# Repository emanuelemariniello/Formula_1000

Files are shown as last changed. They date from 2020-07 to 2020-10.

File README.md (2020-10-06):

# Formula_1000
The aim of this project is to design from scratch a Formula 1000 racing car using mainly standard components easily founded in the market. The design is guided following the F1000 regulations of 2013 and the UNI and ISO design standards. There are different software used during the project, such as Creo, Solidworks, Catia V5 and Siemens NX as CAD software, Matlab and PyCharm as mathematical solver and Ansys Workbench and Altair HyperWorks as FEA software.

# How to use

A full detailed report on the project is in the following link: (https://github.com/emanuelemariniello/Formula_1000/blob/master/Report/Report.pdf).

Python is needed to be installed in your machine.

Download the project and run the file Index.bat and follow the instructions on the terminal to visualize the main design variables related to the different components.

# Overview

### Gearbox Overview
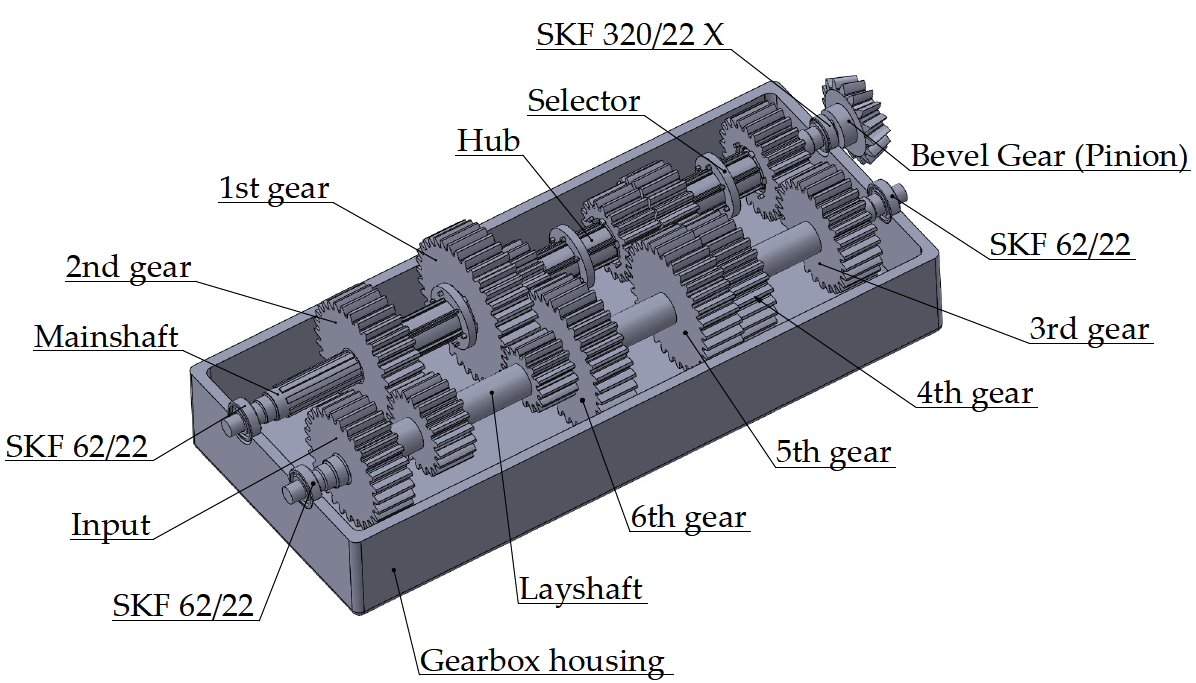
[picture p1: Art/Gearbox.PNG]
Gearbox Overview

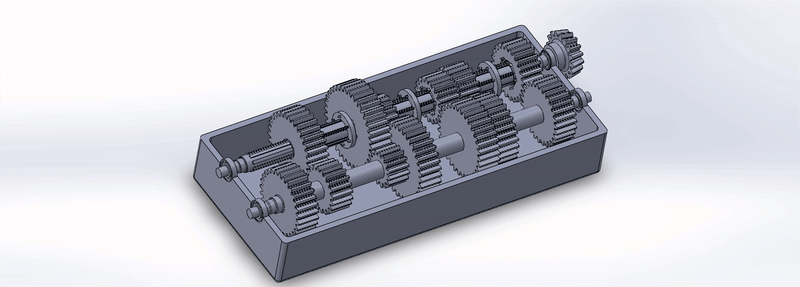
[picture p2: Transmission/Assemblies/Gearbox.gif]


### Open Differential Overview
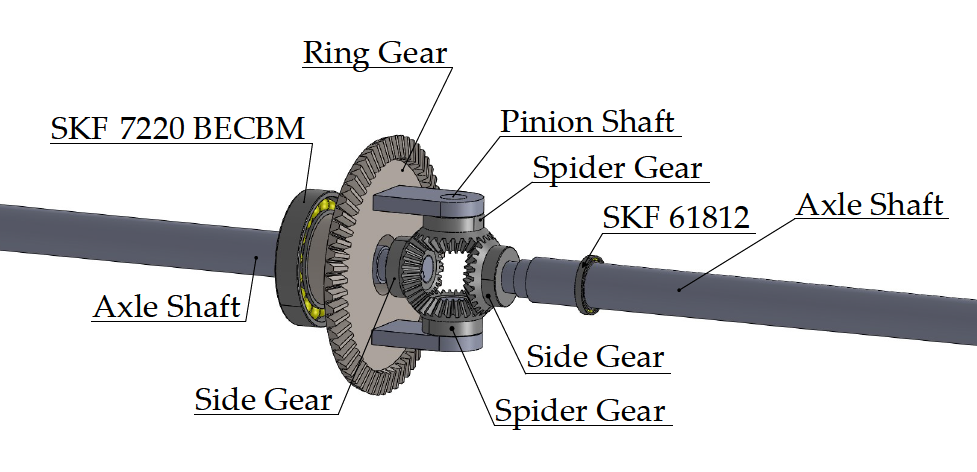
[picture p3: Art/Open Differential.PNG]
Open Differential Overview


### Transmission Overview
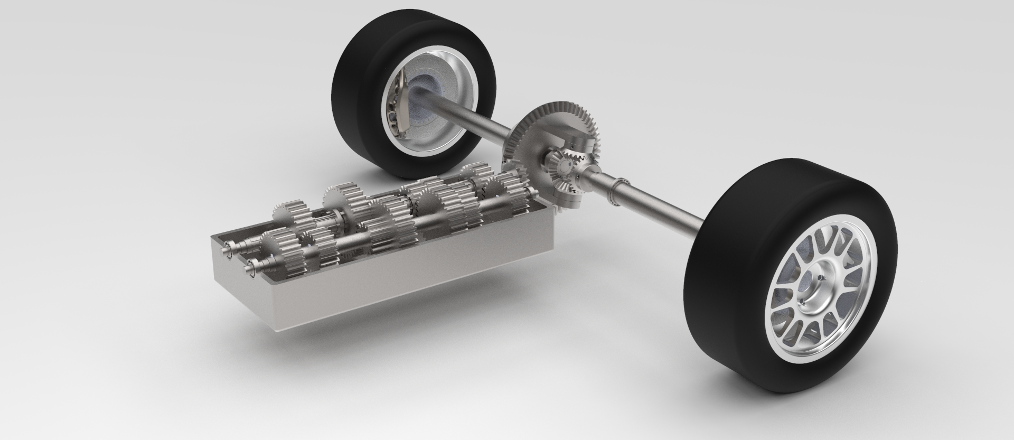
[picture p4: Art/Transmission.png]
Transmission Overview


### Suspensions Overview
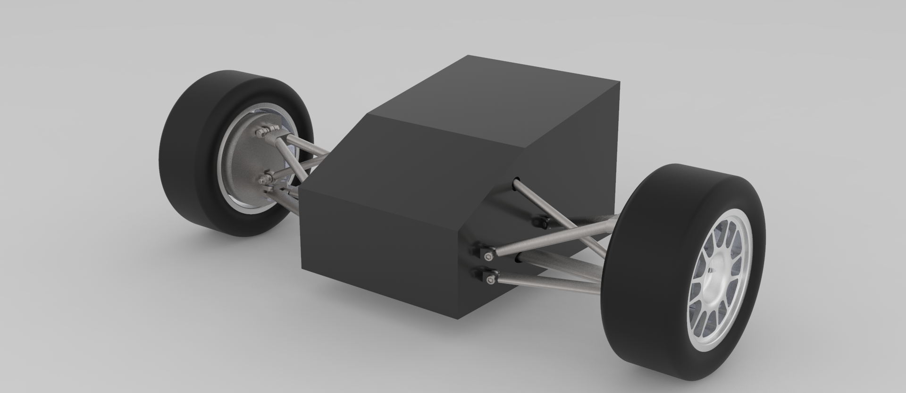
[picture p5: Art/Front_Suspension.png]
Front Suspension Overview

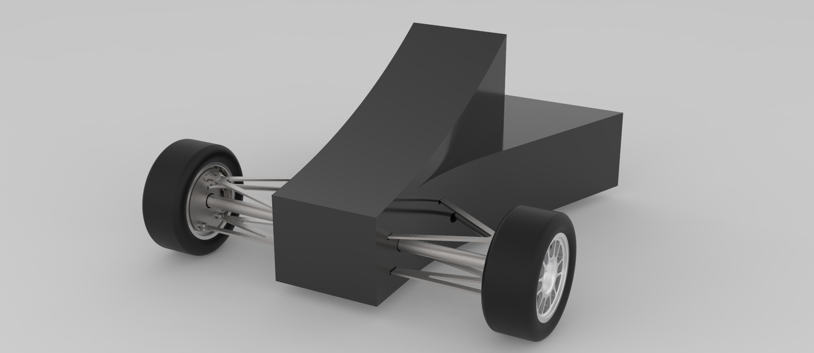
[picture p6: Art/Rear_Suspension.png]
Rear Suspension Overview


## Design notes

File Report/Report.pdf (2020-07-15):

# Design from scratch of a Formula 1000 racing car

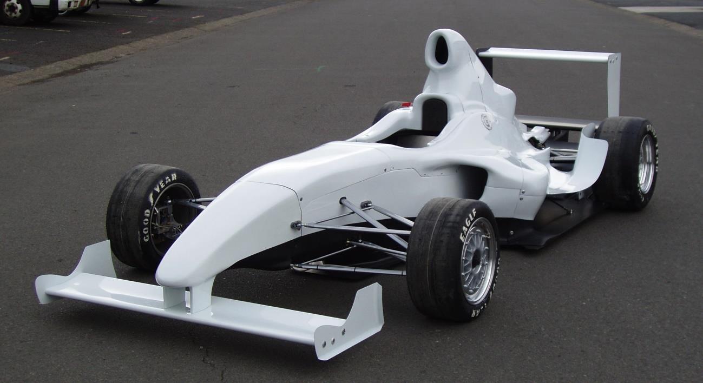
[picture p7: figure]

## Author:

## Emanuele Mariniello

I

## Abstract

The aim of this project is to design from scratch a Formula 1000 racing car using mainly standard components easily founded in the market.
The design is guided following the F1000 regulations of 2013 and the UNI and ISO design standards.
There are different software used during the project, such as Creo, Solidworks, Catia V5 and Siemens NX as CAD software, Matlab and PyCharm as mathematical solver and Ansys Workbench and Altair HyperWorks as FEA software.

II

## Contents

III

## List of Acronyms

- F1000 = Formula 1000
- Kph = Kilometres per hour
- g.r. = Gear ratio
- rpm = Rotation per minut
- TBD = To be defined

Design from scratch of a Formula 1000 racing car

Introduction | 1

## 1. Introduction

Formula 1000 is an open wheel class of Formula car racing, with professional and amateur series worldwide. Formula 1000 gets its name from the 1000 cc superbike engine used to power a single seat, open wheel race car with fully adjustable wings and suspension. The F1000 class, known in SCCA as FB, is similar to racing classes FA (Formula Atlantic) and FC (Formula Continental). In the United States, Formula 1000 races in the North American Formula 1000 Championship presented by American Racer Tire as well as SCCA amateur competition.

Formula 1000 RaceCars can reach speeds in excess of 270 kph; brake and corner beyond 3 g's; and provide a challenge to any driver, engineer, or team.

Figure 1-1 Formula 1000 car [2].

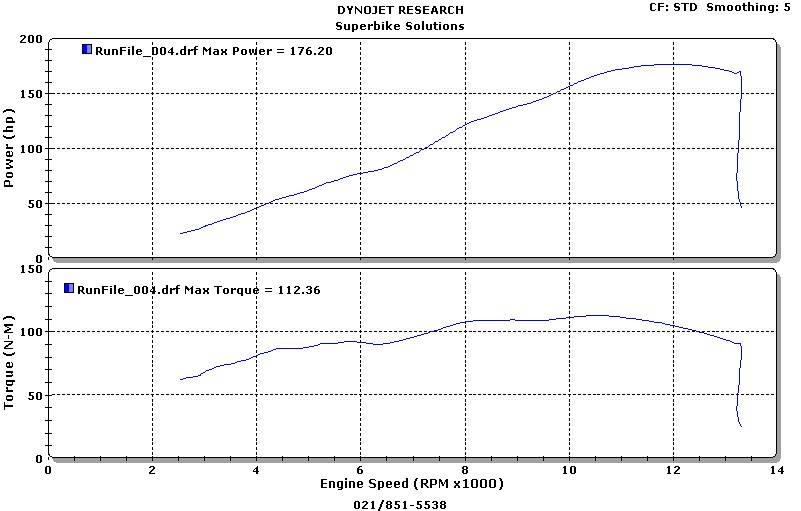
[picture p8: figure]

Engine | 2

## 2. Engine

Following the F1000 regulation of 2013 [1] there are 4 engines that it is possible to select for the racing car, they are:

- Kawasaki ZX10R 1000
- Suzuki GSXR 1000
- Yamaha YZF R1
- Honda CBR 1000 RR

Honda CBR 1000 RR is the engine selected for this project, following there are all the specifications:

Table 1 - CBR 1000 RR Engine specs [4].

Figure 2-1 Dyno chart 2014 CBR1000RR [3].

Capacity | 999.8 cc / 61 cu-cu-in
Bore x Stroke | 76 x 55.1 mm
Cooling System | Liquid cooled
Compression Ratio | 12.3:1
Oil Capacity | 3.7 Litres
Max Power | 133 kW / 178 hp @ 12250rpm
Max Torque | 114 Nm / 84.07 ft.lb @ 10500rpm

Trasmission | 3

## 3. Trasmission

## Sequential Gearbox

Typically a sequential gearbox is installed in racing cars, in this project a sequential gearbox with 6th gears (no reverse gear) is going to be designed using commercial components.

## Design

## 3.1.1.1 Gears

Once decided the engine, it is possible to start to design the sequential gearbox.

Figure 3-1 Overview of the sequential gearbox system [6].
The design of it starts calculating the peak torque at the rear wheels, a python code was created to perform this operation by following the procedure described below, to open it just run the file Index.bat in the main folder and select the following path in the script: Trasmission → Gearbox → Gear ratio.
Defining W as the weight of the racing car, L is the wheelbase and Lr as the distance of the center of mass from the rear wheel (this value in this case is an assumption using as reference a real F1 car) [5], them numerically are equivalent to:

W = 490 ∗ 9.81 = 4806,9 [N]; L = 3500 [mm] Lr = 1787,5 [mm]

From these data, the Static rear axle load WR and the Static front axle load WF are determined:

WR = W ∗

Lr
L

= 4806,9 ∗

1787,5
3250 ≅ 2643,80 [N] | (1)

WF = W ∗

LL
L

= 4806,9 ∗

1462,5
3250 ≅ 2163,10 [N] | (2)

Consequential the Traction force is equal to:

F =

WR ∗ μ

1 −

ℎm ∗ μ
L

=

2643,80 ∗ 1,2

1 −

325 ∗ 1,2
3250
≅ 3605,175 [N] | (3)

Where, μ is the average coefficient of friction between wheels and the road while ℎm is the height of the centre of mass.
Next step is to evaluate the longitudinal load transfer ΔWx:

ΔWx = +̅

F ∗ ℎm
L

= +̅

3605,175 ∗ 325
3250 | ≅ ±360,52 [N] | (4)

So, the Rear wheel loads WRR and WRL are equal to:

WRR, WRL =

WR + ΔWx
2

=

2643,80 + 360,52
2

≅ 1502,16 [N] (5)

While the Front wheel loads WFR and WFL are equal to:

WFR, WFL =

WF − ΔWx
2

=

2163,10 − 466,55
2

≅ 901,3 [N]

(6)

Now it is possible to evaluate the Peak torque rear wheels Twℎeels:

T_wℎeels = (W_RR + W_RL ) ∗ r_w ∗ μ = (1502,15 + 1502,15) ∗ 0,33 ∗ 1,2 ≅ 1190,43 [Nm]

(7)

Twℎeels, is very important because from it starts the defining of the gear ratios of the gear system beginning from the 1st gear ratio.

First thing is to define the minimum total 1st gear ratio, between the engine crankshaft and the wheel driveshafts, able to provide enough torque to the wheels in order to start the movement of the racing car; to do so, the following equation is used:

min total 1

stgear ratio =

Twℎeels

TEngine

(8)

Twℎeels is already defined, TEngine is defined analyzing the engine Dyno chart (Figure 2-1). This value is selected thinking at the torque provided by the engine and at which range of rpm it is available.
This range needs to be big enough to help the driver, at the starting race, to do not have that the car shuts down, but at the same time, this ratio does not need to be too small otherwise the top speed of the 1st gear is low.

Figure 3-2 Tengine Selection.
Selecting TEngine equal to 100 Nm, as it is possible to observe in the Figure 3-2, the rpm range is quite big (from around 7500 rpm to around 12500 rpm) so the engine within this range will provide enough torque and the driver, at the starting of the race, with a proper gear ratio, it will be able to start the race without any problem.
So the minimum total 1st gear ratio is equivalent to:

min total 1

stgear ratio =

Twℎeels

TEngine

=

1190
100 = 11,9 | (9)

The total gear ratio, in the gearbox, is evaluated multiplying every gear ratio per each coupling of gear wheels active; each engaged gear has inside this multiplication the primary gear reduction, between input shaft from the engine and the layshaft (connection visible in the Figure 3-3), the gear ratio of the differential and the relative coupling of gear wheels associated to the gear engaged.

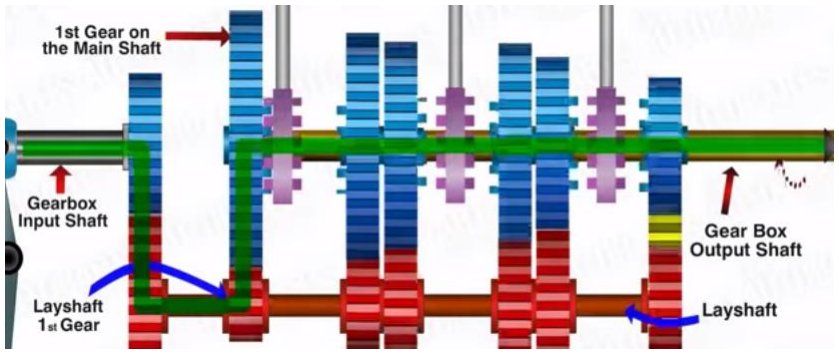
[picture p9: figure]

Figure 3-3 Example of 1

st gear inserted [6].

Using as a reference the same kinds of gearboxes, both the gear ratio of the primary reduction (ipr) and the differential (idifferential) are fixed respectively to 1,8125 and 3,5625, so from these ratios it is possible to find the minimum gear ratio required engaging the 1st gear.

min 1

stgear ratio =

min total 1

stg. r.

(ipr) ∗ (idifferential)

=

11,9
1,8125 ∗ 3,5625
≅ 1,84

(10)

The racing cars use spur gears, also if they tend to vibrate and become noisy at higher speeds, not so important compared to the fact that they have a better way to transmit torque compared to helical gears.
So fixing helix angle β=0° and the pressure angle α=20°
, with the Table 2 is it
possible knowing the gear ratio (u in this table) the minimum number of teeth required for the gears with external teeth (in Italian “Dentatura esterna”), in this case the number is equal to 15, so z1, which represents the number of teeth of the driving gear, is set as 15.

Table 2 - Minimum number of teeth spur gear [7].

The gear ratio (defined as i) selected is 2,4:

z2 = i ∗ z1 = 2,4 ∗ 15 = 36 | (11)

Check that the total 1st gear ratio is greater than the minimum value:

Total 1

stgear ratio = (ipr) ∗ (idifferential) ∗ (i1
st)
= 1,8125 ∗ 3,5625 ∗ 2,4 ≅ 15,4969 > 15,41 | (12)

From this point, it is possible to define the other ratios thinking mainly, but not only, about at which speed the driven reaches before changing gear. The maximum speed, so also the point when it is better to change gear, is reached when the engine is able to provide the maximum torque, in the Honda CBR 1000 RR this happens when it reaches around 13000 rpm (Figure 2-1).
An estimation of the speed that the vehicle can reach at that moment for each gear engaged, can be done using this formula, in this cased used for the 1st gear:

Max speed 1

stgear =

Max power rpm ∗ π ∗ Φwℎeel ∗ 60 1000 ∗ Total 1

stgear ratio = 13000 ∗ π ∗ 0,3302 ∗ 60 1000 ∗ 15,4969 ≅ 52,21 [km⁄ℎ] | (13)

Where Φwℎeel is the diameter of the wheels in meters.
As will be later explained in paragraphs 3.1.1.1.1 and 3.1.1.1.2, by calculating the minimum modulus for each gear coupling, it is established that the modulus of the all the spur gears inside the gear box is fixed at 5. An important constraint in the gearbox system is that the wheelbase between each gear coupling needs to be the same, it can be satisfied by the following calculation:

wℎeelbase 1

stgear =

module ∗ (z1 + z2)
2

=

5 ∗ (15 + 36)
2
= 127,5 [mm]

(14)

Observing the equation (14) to have the same wheelbase, having the same module, the sum of the teeth of the gears coupled must be the same everywhere in the gearbox (except for the primary reduction and the differential), in this case, the sum is equal to 15 + 36 = 51, and the gear ratio is related to the teeth with this expression:

gear ratio =

z2
z1

(15)

So playing with the constraint of the total number of teeth and the maximum speed achieved at the end of the gear before the shift, it is possible to establish every gear ratio. In the project folder called Trasmission there is an excel file called Design.xlsx where it possible to find all the operations explained before, but in the next table is represented directly the final gear ratio output established from it.

| Gear ratio | z1 | z2 | z1+z2 | wheelbase [mm]
Primary reduction | 1,8125 | 16 | 29 | 45 | 112,50
1st | 2,4000 | 15 | 36 | 51 | 127,50
2nd | 1,5500 | 20 | 31 | 51 | 127,50
3rd | 0,8889 | 27 | 24 | 51 | 127,50
4th | 0,7000 | 30 | 21 | 51 | 127,50
5th | 0,5938 | 32 | 19 | 51 | 127,50
6th | 0,5000 | 34 | 17 | 51 | 127,50
Differential | 3,5625 | TBD | TBD | TBD | -

Table 3 - Gear ratios.
At this point is possible design every gear wheel in the gearbox.

## 3.1.1.1.1 Spur Gears

In the project folder Trasmission\Gearbox\Gears\Matlab are present Matlab scripts called Design_xxx_gear.m where all the operations explained in the following paragraph are executed, the procedure design it extracted mainly from the manual “Manuale di Meccanica” [7].
The 1st gear is going to be used as an example case, also because it is the first gear connection where all the necessary data are defined.
Remembering that spur gears are used in a racing gearbox, it is possible to define the helix angle β=0° and the pressure angle α=20° and as defined before the gear ratio i = 2,4. The material selected is the steel C60 (EN 10277-5) with has the ultimate tensile strength σR = 900 [N⁄mm²], the Young modulus E = 217 [GPa]

and the Brinell hardness HB = 215 [HB].
Designing the spur gear wheels to wear-resistant, another evaluation is: how many hours the designed gearbox needs to work before it can have failures? The gearbox needs to survive at least for 6 full grand prix that is around 50 hours in total.
Everything now is specified, so the first step is to calculate the coefficient K1:

K1 ≅ 1,18 ∗ √
E1 ∗ E2
E1 + E2

= 1,18 ∗ √
217 ∗ 217
217 + 217

≅ 388,68 [

√N⁄mm] (16)

both the gear wheels are made with the same material so E1 and E2 are the same. The k constant now is calculated:

k = √
2 ∗ K1

2
z1

2
∗ sin(2 ∗ α)

∗ (1 +

z1
z2

)

3

= √
2 ∗ (388,68)

2
(15)

2 ∗ sin(2 ∗ 20)

∗ (1 +

15
36)

3

≅ 14,36 [√N⁄mm²
3
]

(17)

Now the admissible pressure on the tooth padm can be evaluated:

padm = 24,5 ∗

HB
√n1 ∗ ℎ
6 | = 24,5 ∗

215
√7172,4 ∗ 50 ⁶ | ≅ 625 [N⁄mm²] | (18)

Where ℎ is the minimum working hours of the gearbox, defined before, and n1 is the rotational speed in rpm that is calculated from the gearbox input shaft:

n1 =

ni

ipr

=

13000
1,8125 ≅ 7172,4 [rpm] | (19)

So now it is possible to calculate the minimum module that the gear wheels need to have:

mmin = k ∗ √
T ∗ cos²(β)

λ ∗ padm

2

3

= 14,36 ∗ √
114000 ∗ cos²(0)
10 ∗ (625)

2

3
≅ 4,42 (20)

Where T in the torque provided by the engine in [N ∗ mm] and λ =

b
m

= 10,
where m is module and b is the width of the gear wheels (Figure 3-4). Selecting the module equal to 5, a check needs to be accomplished throught the admissible pressure padm, evaluating the maximum pressure on the side of the tooth pmax:

pmax ≅ K1 ∗ √
2 ∗ T
b ∗ dp1 ∗ sin(2 ∗ α)

∗ (
1

dp1

+

1

dp2

)

= 388,68
∗ √
2 ∗ 114000
50 ∗ (5 ∗ 15) ∗ sin(2 ∗ 20)

∗ (

1
(5 ∗ 15)

+

1
(5 ∗ 36)

)

= 519,54 [N⁄mm²] ≤ 625 [N⁄mm²] = padm

(21)

The check is positive, so means that the module selected is good; inside the equation there are present dp1 and dp2 that they are the pitch diameters respectively of the gear wheel on the layshaft and the gear wheel on the mainshaft.
Evaluating mmin for each gear and checking that pmax ≤ padm, all the gear wheels in the gearbox are verified with a module equal to 5.

Figure 3-4 Spur gear sketch.

## 3.1.1.1.2 Bevel Gears

In the project folder Trasmission\Gearbox\Gears\Matlab is present a Matlab script called Design_differential.m where all the operations explained in the following paragraph are executed, the procedure design it extracted mainly from the manual “Manuale di Meccanica” [7].
The connection between gearbox and differential (the next component towards the wheels) is made up of straight-toothed bevel gears, the case study will be the 6th gear because it has the highest speed among all the gears, defining n1 as the rotational speed of the mainshaft, its rotational speed is equal to:

n1 =

nengine

iprimary ∗ i6
tℎgear

=

13000
1,8125 ∗ 0,5
≅ 14344,8 [rpm] | (22)

The gear ratio of the bevel gears is defined by:

i =

ω1
ω2

=

z2
z1

=

sin δ2
sin δ1

(23)

Where δ2 is the pitch angle of the bevel gear on the driveshaft while δ1 is the pitch angle of bevel gear attached to the mainshaft (so the output from the gearbox), to better understand what they are, the following figure has a representation:

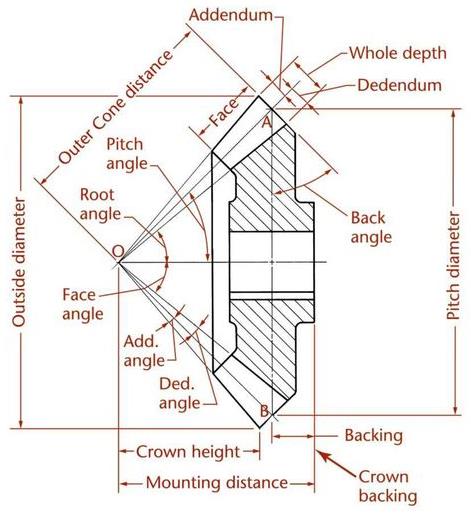
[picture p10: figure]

Figure 3-5 Bevel gears terminology [10].
The gear ratio of the differential is defined in paragraph 3.1.1.1 and is equal to 3,5625 (Table 3) and from it, the variable z1 is assigned the value 16 through the minimum number of teeth allowed by this gear ratio (Table 2).
From the equation (23) also z2 can be evaluated and it is equal to:
z2 = i ∗ z1 = 3,5625 ∗ 16 = 57 | (24)

Now δ2+δ1 = 90°
so from the equation (23) δ2 can be extracted:

i =

sin δ2
sin δ1

=

sin δ2
sin(90 − δ2)

=

sin δ2
cos δ2
==> δ2 = tan⁻¹ (i) = tan⁻¹ 3,5625 ≅ 74,32° | (25)

Consequently δ1 = 90° − 74,32° = 15,68°
Due to the fact that also in this case it will be used the steel C60 to produce the bevel gear wheels K1, as already calculated with the equation (16), is equal to

388,68 [

√N⁄mm].

Next step is to find the constant kc , also in these gear wheels have the pressure angle α = 20°:

kc = √
2 ∗ K1

2
z1

2
∗ sin(2 ∗ α)

∗ (1 +

z1 ∗ cos δ2
z2 ∗ cos δ1

)

3

= √
2 ∗ 388,68²
16² ∗ sin(2 ∗ 20)

∗ (1 +

16 ∗ cos(74,32)
57 ∗ cos(15,68)

)

3

≅ 12,56

(26)

The admissible pressure on the tooth padm is evaluated with the equation (18):

padm = 24,5 ∗

HB
√n1 ∗ ℎ
6 | = 24,5 ∗

215
√14344,8 ∗ 50 ⁶ | ≅ 556,75 [N⁄mm²] (27)

The average module of the bevel gear wheels is equal to:

mm = kc ∗ √
T ∗ ξ ∗ cos²(δ1
)

λm ∗ padm

2

3

= 12,56 ∗ √
114000 ∗ 1,4 ∗ cos²(15,68) 5 ∗ (556,75)

2

3
≅ 5,74

(28)

Where ξ is the corrective coefficient equal to 1,4 for common gears, and the average λm =

b
mm

= 5.

So a standard module equal m = 6 is assumed, mm accordingly to the assumption becomes:

mm =

m
(1 +

λm
z1

∗ sin δ1)

=

7
(1 +

5
16 ∗ sin(15,68))
≅ 5,53 | (29)

A check of the pressure on the tooth needs to be performed:

pmax ≅ K1 ∗ √
2 ∗ T ∗ ξ ∗ cos δ1
b ∗ mm ∗ z1 ∗ sin(2 ∗ α)

∗ (

cos δ1
mm ∗ z1

+

cos δ2
mm ∗ z2

)

= 388,68
∗ √
2 ∗ 114000 ∗ 1,4 ∗ cos(15,68) 35 ∗ (5,53 ∗ 15) ∗ sin(2 ∗ 20)

∗ (
cos(15,68)
(5,53 ∗ 16)

+

cos(74,32)
(5,53 ∗ 57)

)

≅ 554,29 [N⁄mm²] ≤ 556,75 [N⁄mm²] = padm

(30)

The check is positive.

## 3.1.1.2 Layshaft

Once all the gear wheels are defined, it is possible to determinate all the loads acting on them using the following equations from the spur gears:

St =

2 ∗ T
dp
(tangential load in N) | (31)
Sr = St ∗ tan α (radial load in N) | (32)

S = √St
2 + Sr
2 | (33)

Figure 3-6 Loads exchanged between spur gear wheels.
In the next table there is the summary of all the loads applied to the layshaft.

Layshaft
| St [N] | Sr [N] | S [N]
Primary | 1572,41 | 572,31 | 1673,33
1st | 3040,00 | 1106,47 | 3235,10
2nd | 2280,00 | 829,85 | 2426,33
3rd | 1688,89 | 614,71 | 1797,28
4th | 1520,00 | 553,23 | 1617,55
5th | 1425,00 | 518,66 | 1516,45
6th | 1341,18 | 488,15 | 1427,25

Table 4 - Gear loads applied to the layshaft.

The lengths of the beam and the positions of the gear wheels are represented in the following figure:

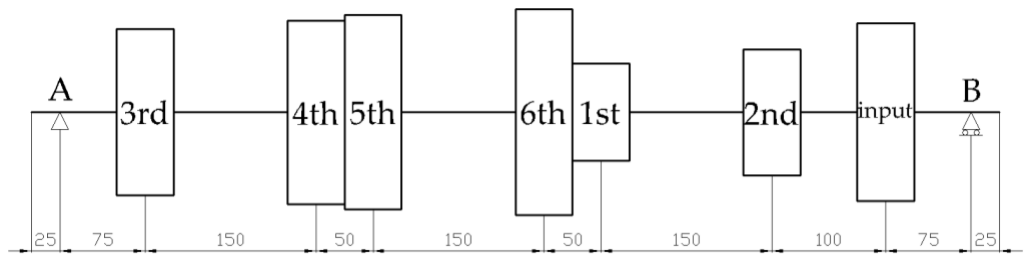
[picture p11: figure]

Figure 3-7 Layshaft sketch.
Studying as an example the case that the 1st gear is engaged, the other gears cases are very similar to this one it changes only the position of S that always remains between the bearing A and the input load. The beam representation will be as following:

Figure 3-8 Layshaft 1

st gear beam representation.

To calculate le bearings loads (Fay and Fby) is enough to perform a beam analysis, the following equations are going to show the generic approach for this kind of load configuration:
{
Fby =

(−Si ∗ lia) + (Sx ∗ lxa)

lab
Fay = Sx − Si − Fby

(34)

lia is the distance between the input load and the bearing A; lxa is the distance between the gear load and the bearing A; lab is the distance between the two bearings; Sx is the gear load and Si
is the input load.
In the project folder Trasmission\Gearbox\Shafts\Python\Lay_shaft, there is Python script called Lay_shaft.py that it analyzes every gear case and they plot the shear chart and the bending moment chart.
Following there is the analysis of the 1st gear case, that is represented in Figure 3-8:
{
Fby =

(−1673,33 ∗ 725) + (3235,10 ∗ 475)
800

≅ 404,38 [N]
Fay = 3235,10 − 1673,33 − 404,38 ≅ 1157,38 [N]

(35)

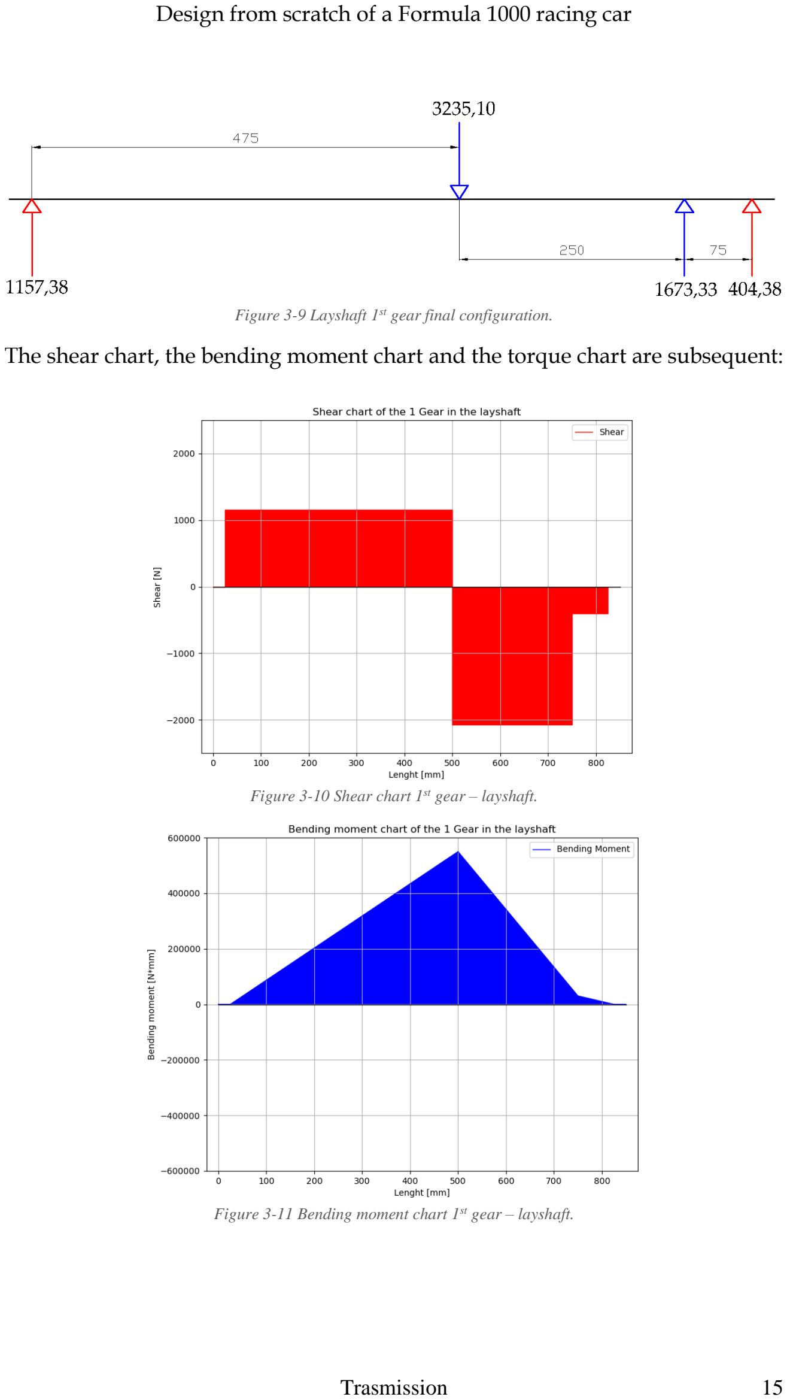
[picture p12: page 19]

Figure 3-9 Layshaft 1

st gear final configuration.

The shear chart, the bending moment chart and the torque chart are subsequent:

Figure 3-10 Shear chart 1

st gear – layshaft.

Figure 3-11 Bending moment chart 1

st gear – layshaft.

Figure 3-12 Torque chart 1

st gear – layshaft.

From these charts it is possible to design the layshaft evaluating the minimum section diameters that the shaft needs to have, from them it is noticed that the situation in the input gear wheel and in the 1st gear wheel are really different and the magnitude of both shear and bending moment in the 1st gear wheel are much higher, so the minimum diameter will be evaluated from that section (l = 500 [mm] and Mb = 549757,73 [N ∗ mm]).
This shaft transmits torque and, at the same time, not negligible bending moments consequently the sizing needs to be done by flexion-torsion, so the first step is to calculate the ideal bending moment Mbi
:

Mbi = √Mb
2 + 0,75 ∗ T

2 = √549757,73² + 0,75 ∗ 114000²

≅ 558552,2 [N ∗ mm]

(36)

From the equation of the section modulus of a circular section, it is possible to obtain the minimum diameter:

d = √
32 ∗ Mbi

π ∗ σadm,f

3
(37)

Having σadm,f =

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
= 150 [MPa], where σU is the ultimate strength in MPa of the steel C60 and X is a safety factor, so now d is equal to:

d = √
32 ∗ 558552,2
π ∗ 150

3
≅ 33,59 [mm]

(38)

Evaluating all the other cases, the minimum diameters in the same section are:

Gear case | D [mm]
1st | 33,59
2nd | 25,83
3rd | 21,58
4th | 25,59
5th | 25,72
6th | 25,91

Table 5 - Minimum layshaft diameter per each gear case.
The middle section of the layshaft needs to be at least 34 mm, picking the subsequent integer number of the highest value among all the minimum diameters indicated in Table 5.
Another consideration is how to join the gear wheels to the layshaft, to do so, keys are used, so the diameter of the layshaft must be increased more in order to satisfy that the minimum diameter is 34, explained in the following figure:

Figure 3-13 Section with keyway representation.

From the ISO R773, the key can be selected:

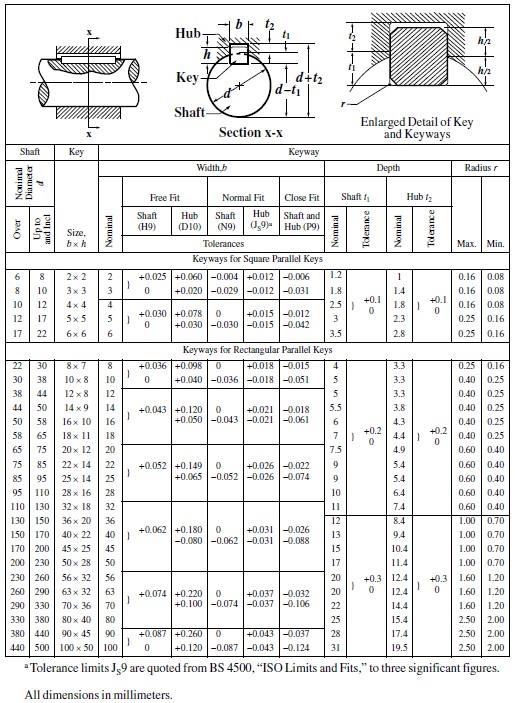
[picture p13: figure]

Figure 3-14 ISO R773 [8].
The minimum diameter is between 30 and 38 mm, so the keyway depth is 5, consequently remembering that the minimum diameter is 34 mm means that the external diameter must be at least 39 mm but in doing so the diameter no longer falls within the range 30 - 38 mm, then the selection must be within the range 38
- 44 mm, here the keyway depth is always 5, therefore the selection of an external diameter equal to 40 mm satisfies all the required requirements.
All the dimensions related to the key are summarized in the following table:
d | 40 mm
b | 12 mm
h | 8 mm
t1 | 5 mm
t2 | 3,3 mm

Table 6 - Key dimensions.

Now it is necessary to define the diameters at the ends of the shaft, where the bearings will be housed, these diameters depend from the bearings but due to the fact that the loads are not so high the bearings will be small.
It is not good to have a very huge difference between the diameters because there are some design rules to respect, such as that the increase of the diameter, or decreasing of it, between two consecutive section needs to be maximum 20%, using an equation if there is an increasing of the diameter:
d2 ≤ d1 ∗ 1,2 | (39)

Where d1 is the diameter of the previous section and d2 is the consegutive diameter.
The diameter selected to the ends is equal to 22 mm, so the bearings now can be selected, going through the SKF website it is possible to visualize the bearings catalogue, here what is needed are radial ball bearings with the internal diameter equal to 22 mm, since the loads have only the radial component and the rotational speed is high, and from that list the Bearing SKF 62/22 it is selected with the following characteristics:

Figure 3-15 SKF 62/22 Technical specification [9].
Once selected the bearings they need to be verified, a python script called Bearings_lay_shaft.py is present inside the project folder Trasmission\Gearbox\ Bearings\Python an it performs this operation.
The first operation is to calculate the millions of revolutions that the bearing needs to perform at least before it needs to be replaced, so after 50 hours, (with 10 percent of failure), the equation is equal to:

L10 =

nlaysℎaft ∗ ℎ ∗ 60
1000000 =

13000
1,8125 ∗ 50 ∗ 60

1000000
≅ 21,52 [mln of revolutions]

(40)

Assuming that the speed of the layshaft is constant with the maximim speed (to have the worst case possible), the most important variable to look at becomes the bearing load and the 3rd gear has the highest loads in magnitude and in particular Fay (Fay = 1,47191 [kN]).
Now, the basic dynamic load rating C needs to be evaluated:

C = √L10

3

∗ Fay = √21,52 ³
∗ 1,47191 ≅ 4,1 [kN] | (41)

The basic dynamic load rating of the SKF 62/22 bearing is equal to 14 [kN] so the bearing can operate in both ends of the shaft without any problem.
Now everything is defined and the final technical drawing of the layshaft can be found in the project folder Trasmission\Gearbox\Shafts\Creo\Lay_shaft.

## 3.1.1.3 Mainshaft

The mainshaft design is similar to the layshaft design, paragraph 3.1.1.2, where the equations are already explained so they will not be explained again but used directly.
The loads applied on the main shaft from the spur gear wheels are defined as the equations (30), (31) and (32), but those from the bevel gear wheels they are slightly different:

St =

2 ∗ T
dm
(tangential load in N) | (42)
Sr = St ∗ tan α ∗ cos δ (radial load in N) | (43)
Sa = St ∗ tan α ∗ sin δ (axial load in N) | (44)

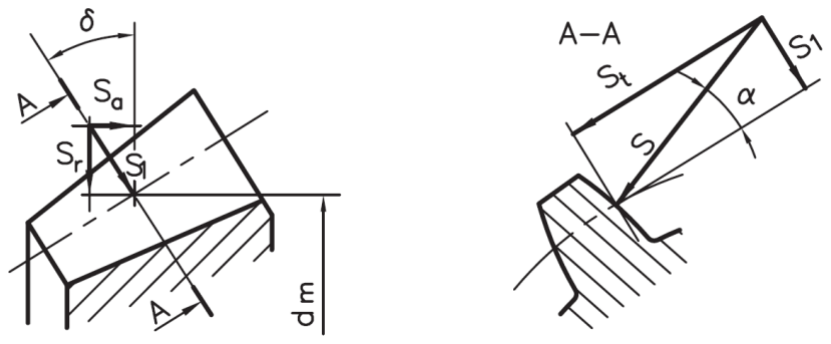
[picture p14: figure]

Figure 3-16 Loads exchanged between bevel gear wheels.

The loads applied on the mainshaft from the bevel gear wheels are S = √St
2 + Sr
2
and Sa, in the next table there is the summary of all the loads applied to the mainshaft from all the gear wheels:

Mainshaft
| Sa [N] | S [N]
1st | 0 | 1347,96
2nd | 0 | 1565,37
3rd | 0 | 2021,94
4th | 0 | 2310,79
5th | 0 | 2554,03
6th | 0 | 2854,50
Differential | 253,35 | 2729,14

Table 7 - Gear loads applied to the layshaft.
The lengths of the beam and the positions of the gear wheels are represented in the following figure:

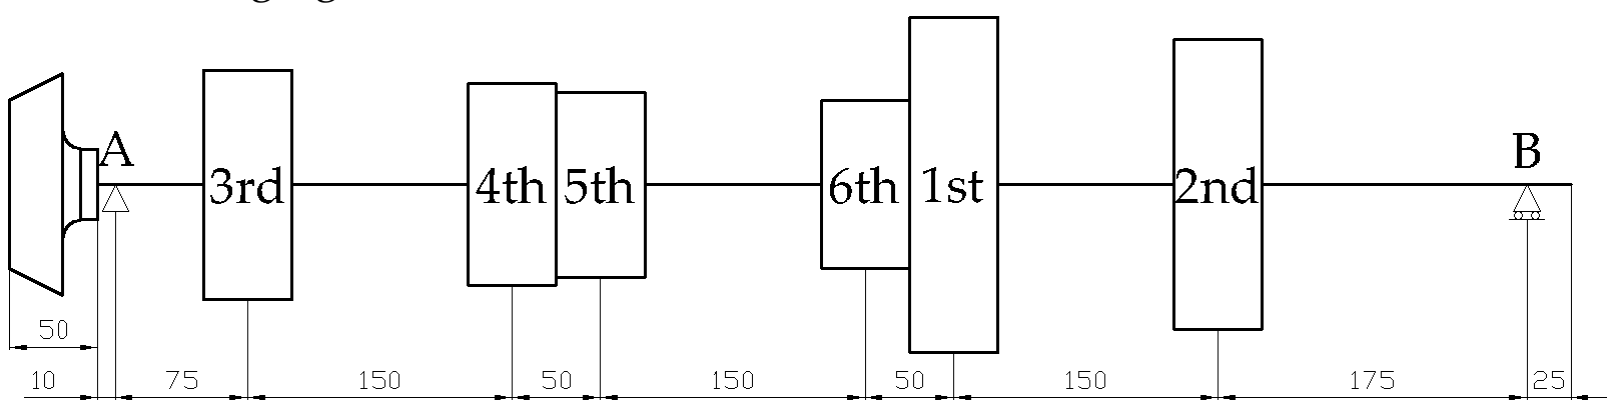
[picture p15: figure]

Figure 3-17 Mainshaft sketch.
As in the paragraph 3.1.1.2, the example case is when the 1st gear is engaged, the other gears cases are similar as the case of the layshaft indeed the position of S is always between the bearings but in this case, compared to the previous one, there is not input load but there are two loads (both radial and axial) from bevel gear in the other side of the beam.
The beam representation will be as following:

Figure 3-18 Mainshaft 1

st gear beam representation.

Sx and Sy are the loads from the bevel gear wheel while S1 is from the 1st spur gear and in A, due to the fact that the bevel gear wheel is providing an axial load, there is a necessity to insert an angular bearing.
Again, as it was for the layshaft, to calculate le bearings loads (Fax, Fay and Fby) is enough to perform a beam analysis, the following equations are going to show the generic approach for this kind of load configuration:

{

Fby =

(−Si ∗ lia) + (−Sy ∗ loa)

lab
Fay = Sy − Si − Fby

Fax = Sx

(45)

lia is the distance between the spur gear load and the bearing A; loa is the distance between the bevel gear load and the bearing A and lab is the distance between the two bearings.
So for the 1st gear, represented in Figure 3-18, the numerical procedure is:

{

Fby =

(−1347,96 ∗ 475) + (−2729,14 ∗ 45)
800

≅ −953,86 [N]
Fay = 2729,14 − 1347,96 − (−953,86) ≅ 2335,04 [N] Fax ≅ 253,35 [N]

(46)

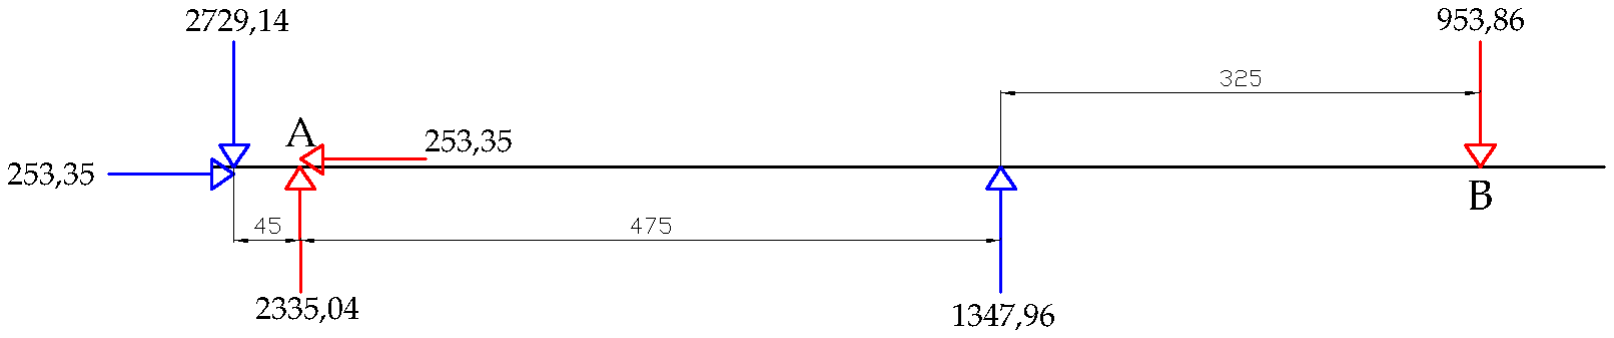
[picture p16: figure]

Figure 3-19 Mainshaft 1

st gear final configuration.

The shear chart, the bending moment chart, the traction chart and the torque chart are subsequent:

Figure 3-20 Shear chart 1

st gear – mainshaft.

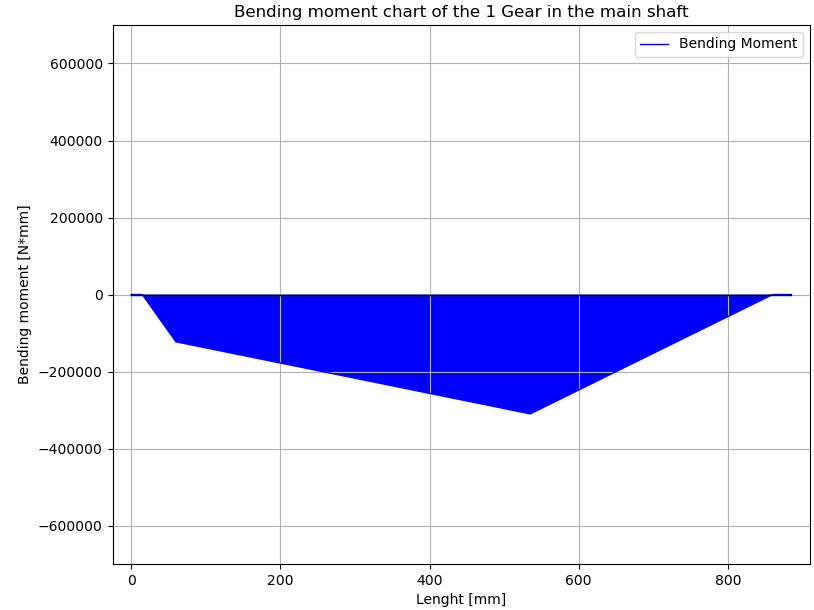
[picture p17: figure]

Figure 3-21 Bending moment chart 1

st gear – mainshaft.

Figure 3-22 Traction chart 1

st gear – mainshaft.

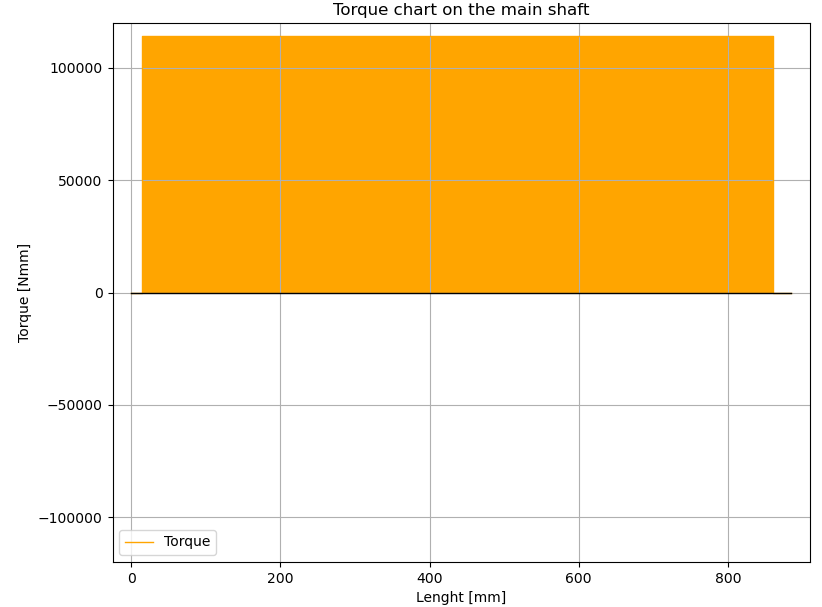
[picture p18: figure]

Figure 3-23 Torque chart 1

st gear – mainshaft.

As already explained in paragraph 3.1.1.2, from these charts it is possible to extract data in order to design the mainshaft evaluating the minimum sections diameters that the shaft needs to have.
The critical sections are located in the bearing A and where is installed the spur gear. The mainshaft, similar the layshaft case, transmits torque and not negligible bending moments at the same time so the sizing is done by flexion-torsion.
The calculation of the ideal bending moment Mbi in the spur gear section is displayed here:

Mbi = √Mb
2 + 0,75 ∗ T

2 = √310005,99² + 0,75 ∗ 114000²

≅ 325347,07 [N ∗ mm]

(47)

From the equation of the section modulus of a circular section, it is possible to obtain the minimum diameter:

d = √
32 ∗ Mbi

π ∗ σadm,f

3
(48)

Having σadm,f =

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
= 150 [MPa], where σU is the ultimate strength in MPa of the steel C60 and X is a safety factor, so now d is equal to:

d = √
32 ∗ 325347,07
π ∗ 150

3
≅ 28,06 [mm]

(49)

With the same procedure, the minimum section diameter in the bearing A area can be evaluated, being that in every case the bending moment is always the same, the value is always equal to:

Mbi = √Mb
2 + 0,75 ∗ T

2 = √122811,39² + 0,75 ∗ 114000²

≅ 157574,23 [N ∗ mm]

(50)

d = √
32 ∗ Mbi

π ∗ σadm,f

3

= √
32 ∗ 157574,23
π ∗ 150

3
≅ 22,03 [mm] | (51)

Evaluating all the other cases, the minimum diameters in the spur gear section are:

Gear case | D [mm]
1st | 28,06
2nd | 26,05
3rd | 26,29
4th | 31,77
5th | 33,43
6th | 35,04

Table 8 - Minimum mainshaft diameter per each gear case in the spur gear section.

Unlike the layshaft, in this case, a the middle section of the mainshaft needs to be with a straight-sided spline section, it must be designed following the ISO 14-82, showed in the following figure:

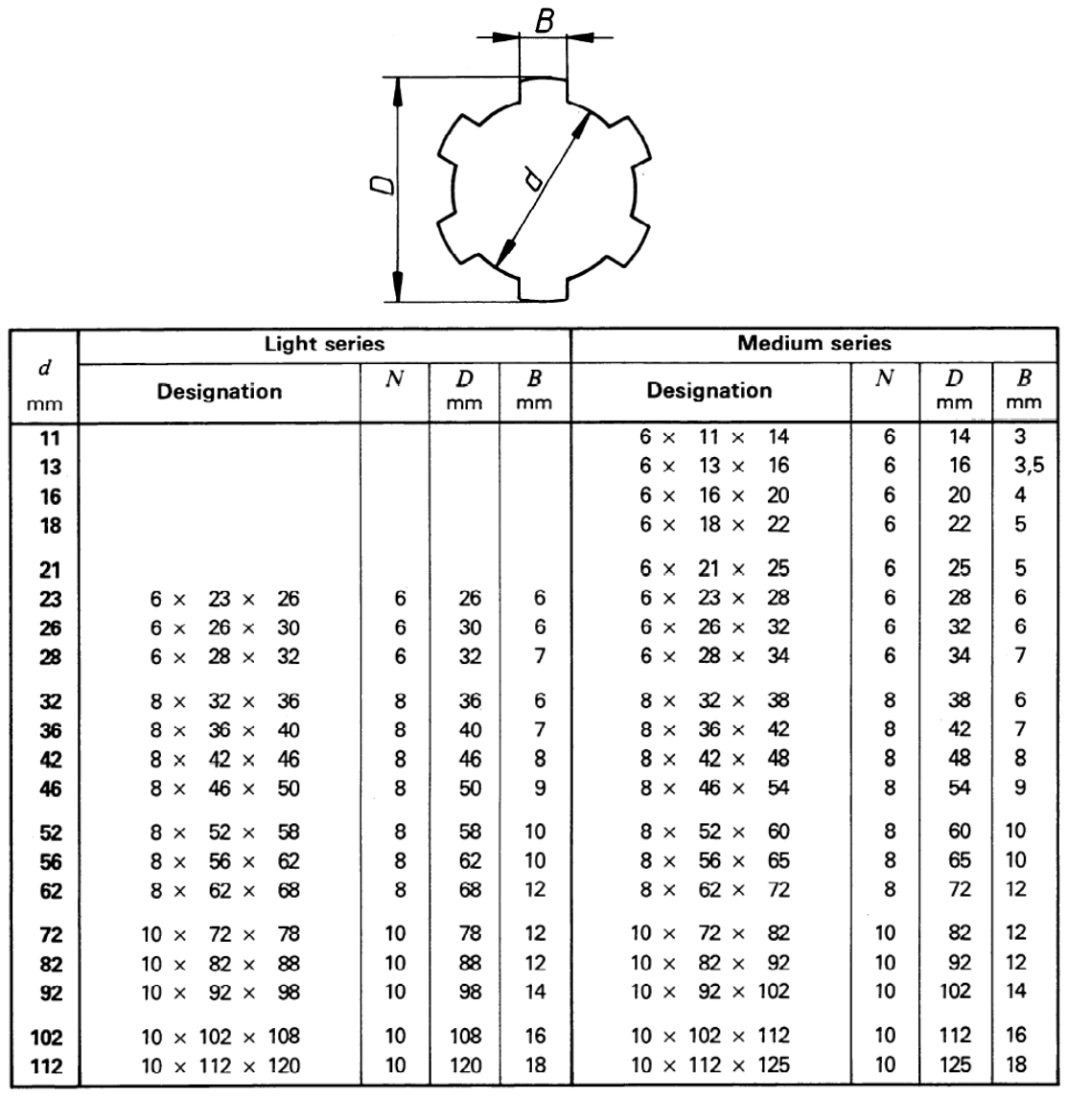
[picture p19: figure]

Figure 3-24 ISO 14-82 [11].
Being the maximum value of the minimum diameter is equal to 35,04 mm (Table 8), observing Figure 3-24, the first standard value suitable is 36 mm so selecting the light series the following dimensions can be picked:
d | 36 mm
D | 40 mm
B | 7 mm
N | 8

Table 9 - Straight-sided spline dimensions.

Knowing the minimum diameter of the shaft section in correspondence of the bearing A, the bearing can be selected and verified. The bearing A, having the axial load, must be a tapered roller bearing with a diameter at least 22 mm.
The selection of the tapered roller bearing is similar to the deep groove ball bearing one, the example case is going to be used the 2nd gear because it has the highest loads on the bearing A, that they are equal to:
Fay = 2,54023 [kN]; Fax = 0,25335 [kN] | (52)

About the rotational speed of the mainshaft is equivalent to:

nmainsℎaft =

nengine
gear ratio2
nd

=

13000
2,809375 ≅ 4627,36 [rpm] (53)

The total load applied on the bearing is:

Fa = √Fay
2
∗ Fax

2 = √2,54023 ² + 0,25335² ≅ 2,5528 [kN] (54)

Using the equation (40) it is possible to calculate the number of revolutions that the bearing needs to support for the minimum hours of service required:

L10 =

nmainsℎaft ∗ ℎ ∗ 60
1000000 =

4627,36 ∗ 50 ∗ 60
1000000
≅ 13,88 [mln of revolutions]

(55)

In this case, the speed of the mainshaft is not constant but it is assumed that it is always rotating at the maximum speed to have the worst scenario possible. Assuming what it is described before, the basic dynamic load rating C needs to be evaluated using the equation (41) moreover remembering that this bearing is made with rollers and not with balls, the index of the root is not anymore 3 but 10
3

⁄ :

C = √L10

10
| 3

⁄
∗ Fa = √13,88

10
| 3

⁄
∗ 2,5528 ≅ 5,62 [kN]

(56)

The SKF 320/22 X is the tapered roller bearing selected from C (Basic dynamic load rating) and the technical specifications are displayed in the next figure:

Figure 3-25 SKF 320/22 X Technical specification [12].
The basic dynamic load rating of the tapered roller bearing SKF 320/22 X is equal to 30,9 [kN] and its limiting rotational speed is equal to 15000 [rpm], so it is able to support the worst case that it is the 6th gear with 14344,82 [rpm].
Also in the position B needs to be selected and verified the bearing, that is going to be a deep ball bearing; for this bearing the worst case, both in the point of view of load and speed, is the 6th gear, where the load is equal to:
Fby = 1,66996 [kN] | (57)

And the mainshaft rotational speed is:

nmainsℎaft =

nengine
gear ratio6
tℎ

=

13000
0,90625 ≅ 14344,82 [rpm] (58)

The millions of revolutions performed by the bearing before it needs to be replaced (assuming it is going at the maximum speed all the time), is equivalent to:

L10 =

nmainsℎaft ∗ ℎ ∗ 60
1000000 =

14344,82 ∗ 50 ∗ 60
1000000
≅ 43,03 [mln of revolutions]

(59)

As the equation (41), the basic dynamic load rating C is:

C = √L10

3

∗ Fay = √43,03 ³
∗ 1,66996 ≅ 5,85 [kN] | (60)

As for the layshaft, the Bearing SKF 62/22 respects all the requirement so it can be selected, in the Figure 3-15 there are all the technical specification of it.

Now everything is defined and the final technical drawing of the mainshaft can be found in the project folder Trasmission\Gearbox\Shafts\Creo\Main_Shaft and a python script in the project folder Trasmission\Gearbox\Bearings\Python called Bearings_main_shaft.py performs all these operations.

## 3.1.1.4 Extra components

Installed with the mainshaft, there are some other extra components that are:

- Hubs;
- Needle roller bearings;
- Deep groove ball bearings;
- Selectors.

The hub is a longitudinally drilled cylinder with the same straight-sided spline

profile as the mainshaft, where at the ends of the external diameter it acts as a

housing for the needle roller bearings and the deep groove ball bearings, while

in the middle part present custom straight-sided spline profile that works as a

guide for the selector.

There are three different hubs in the gearbox, which only have different section

lengths based on the position they will occupy in the shaft, one of them is shown

in the following figure:

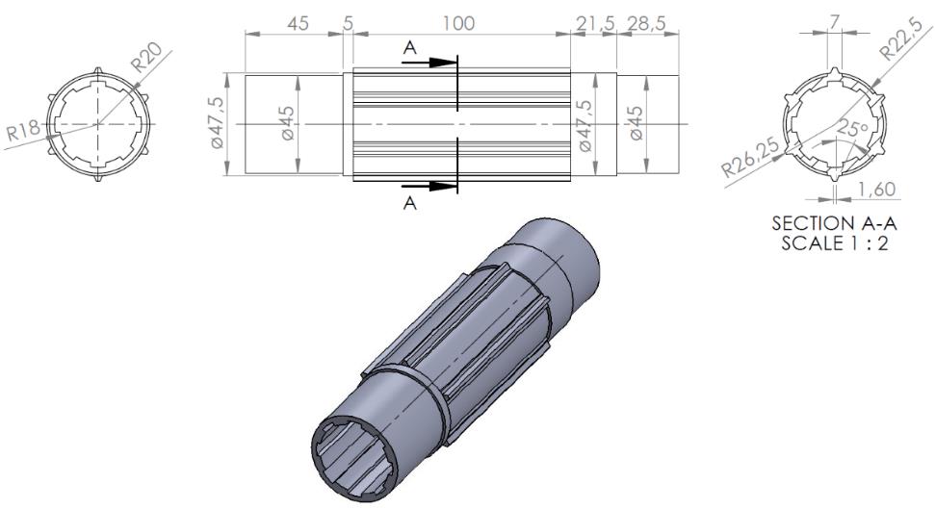
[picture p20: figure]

Figure 3-26 Hub 1 - Technical drawing.

All the spur gears on the mainshaft are not directly fixed to it but rotate freely

until the selector creates a connection with the mainshaft which subsequently

rotates at the same speed as the gear, the procedure with which it occurs will be

explained later.

The important point is that all the gear wheels, in the mainshaft, need to have a

needle roller bearings in order to rotate.

This bearings are located between the hub and the gear wheel, in this case the

main challenge to select them is due to the high speed of the 6th gear, not easy to

solve because the bearing is quite big in diameter (the internal diameter is equal

to 45 mm, see the Figure 3-26). To solve this problem in the first three gears (with

a rotational speed lower than 10000 rpm) the needle roller bearing RNAO

45x62x40 is installed (Figure 3-27) while in the rest of the gears is installed the

deep groove ball bearings SKF 61809-Y (Figure 3-28).

Figure 3-27 RNAO 45x62x40 Technical specification [13].

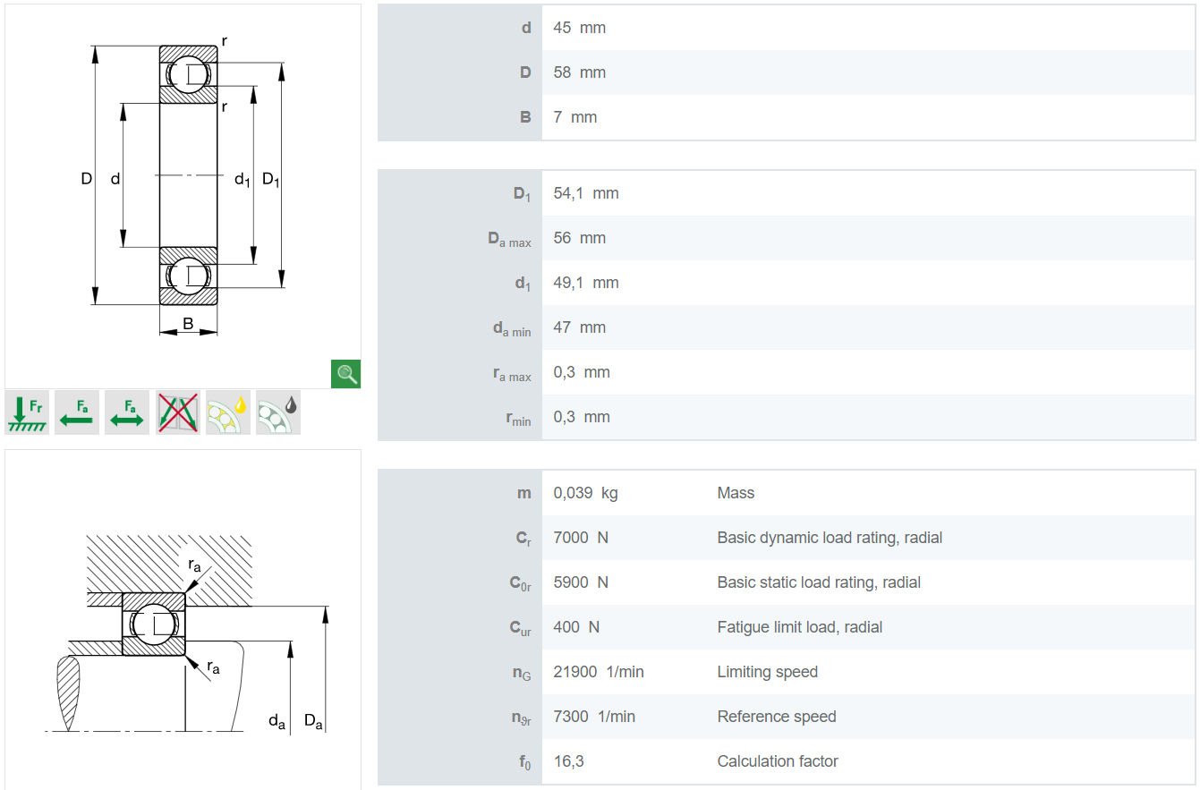
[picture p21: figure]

Figure 3-28 SKF 61809-Y Technical specification [14].
The selector slides on the central external toothing of the hub which, activated by

a special shaft, allows, through the contact of two lateral teeth one placed on the

spur gear while the other on the selector itself, to define which gear wheels are

active at that moment. Also for this component, there are three different versions

based on the gear wheels with which the component will interact, in the next

figure there is the representation of the selector between the 1st and 2nd gear:

Figure 3-29 Disk 1

st
- 2

nd
- Technical drawing.

## Finite element analysis

In this paragraph there are some example case showing the stress analysis and deformation analysis.

## 3.1.2.1 Layshaft

The example case here is the 1st gear, as already studied in the paragraph 3.1.1.2.

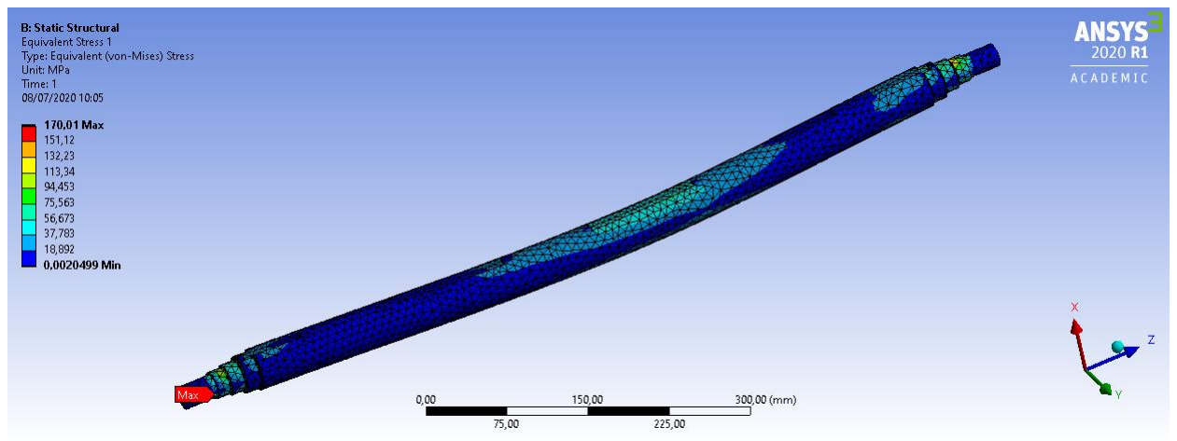
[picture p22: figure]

Figure 3-30 Stress analysis - Layshaft (1st gear).

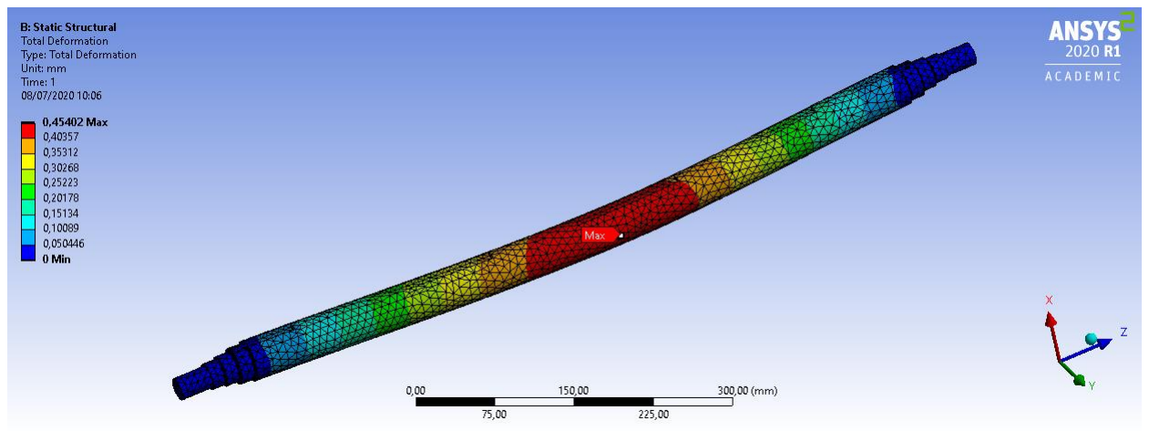
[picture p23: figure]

Figure 3-31 Deformation analysis - Layshaft (1st gear).

In the next table is represented the maximum stress and the maximum displacement in each gear:

Layshaft
| Stress [Mpa] | Displacement [mm]
1 st | 170,01 | 0,226
2 nd | 71,598 | 0,077
3 rd | 78,666 | 0,014
4 th | 117,48 | 0,076
5 th | 111,77 | 0,086
6 th | 83,335 | 0,093

Table 10 - Stress and displacement in the Layshaft.

## 3.1.2.2 Mainshaft

Also in this shaft the example case is the 1st gear, as already studied in the paragraph 3.1.1.3.

Figure 3-32 Stress analysis - Mainshaft (1st gear).

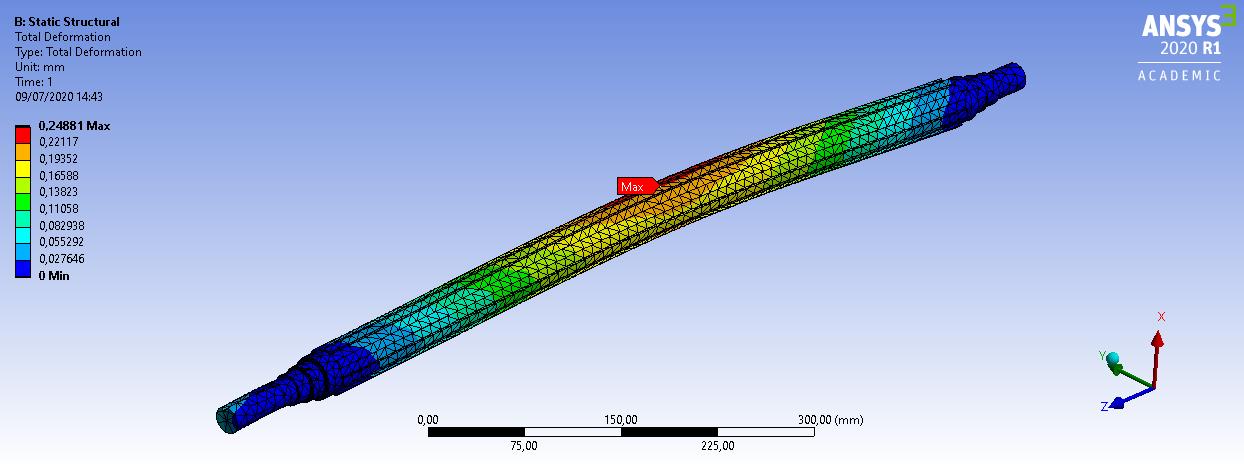
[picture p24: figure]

Figure 3-33 Deformation analysis - Mainshaft (1st gear).

In the next table is represented the maximum stress and the maximum displacement in each gear:

Mainshaft
| Stress [Mpa] | Displacement [mm]
1st | 148,08 | 0,248
2nd | 148,01 | 0,160
3rd | 148,10 | 0,073
4th | 148,26 | 0,296
5th | 148,30 | 0,392
6th | 148,27 | 0,522

Table 11 - Stress and displacement in the Mainshaft.

## Overview

In the next figure there is an overview of all the components inside the gearbox:

Figure 3-34 Gearbox overview.

## Differential

An open differential is installed in the vehicle.
In the project folder Trasmission\Open Differential\Python, two python scripts called Axle_shaft.py and Bearings.py perform all the different operations that are explained in the following paragraphs.

## Design

In this paragraph is described the design of the axle shaft and the selection of the bearings, the design of the bevel gears (Pionion gear and Ring gear) are already explained in the paragraph 3.1.1.1.2.

The core of the differential is compose with 4 Miter Gears KHK SMA4 25, with a gear ratio equal to 1, the gear wheel is represented in Figure 3-35:

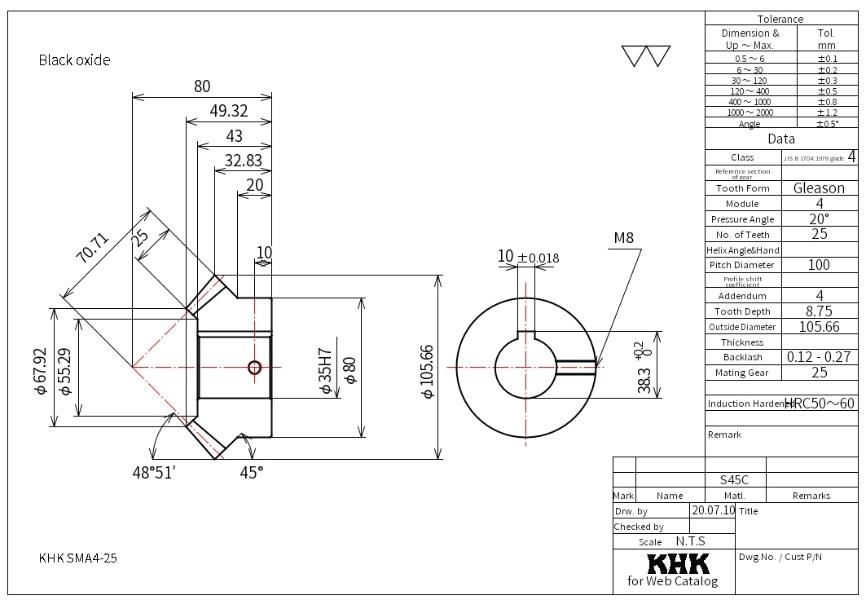
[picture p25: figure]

Figure 3-35 Miter Gears KHK SMA4 25 [17].
The differential can be divided into two parts (Differential side and Shaft side), the Differential side is more stressed so it will be the study case used to perform the design and the solution found will be applied also in the Shaft side (Figure 3-36).

Figure 3-36 Differentil Side / Shaft Side.

To simplify the study case, the loads from the Ring gear are directly applied on the axle shaft (the shaft where the wheels are connected), so the beam is represented as follows:

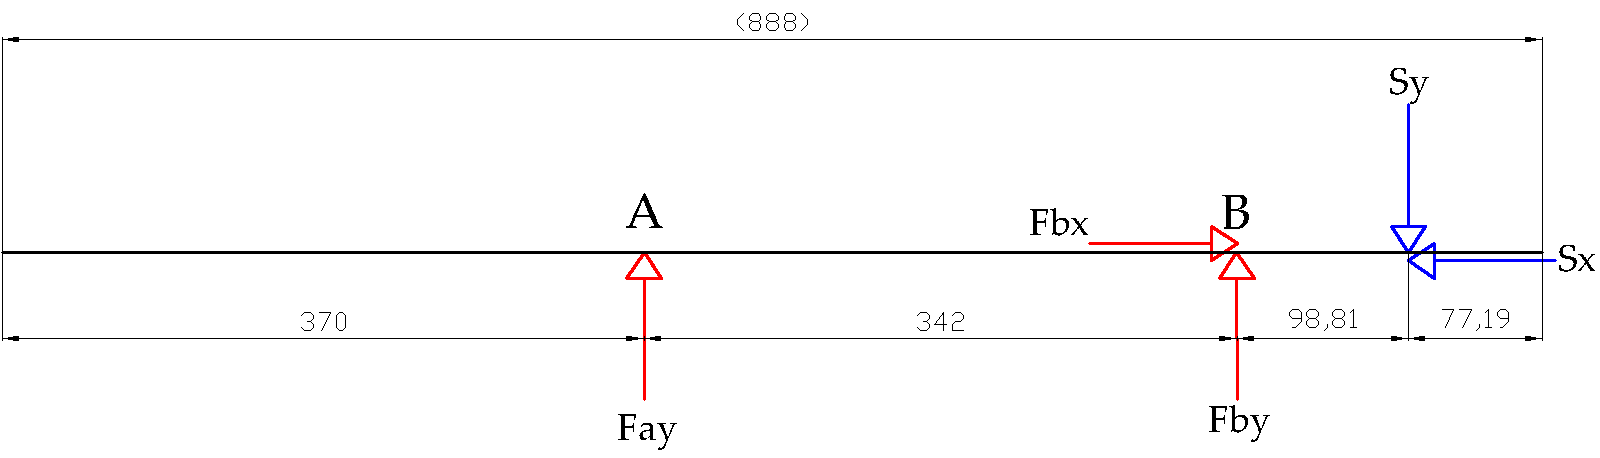
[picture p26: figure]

Figure 3-37 Axle shaft beam representation.
Sx and Sy are the loads from the Ring gear while Fay, Fbx and Fby are bearings loads; the beam analysis equations are the following:

{

Fay = −

Sy ∗ 98,81
342 = −

726,46 ∗ 98,81
342

≅ −209,89 [N]
Fby = Sy − Fay = 726,46 − (−209,89) ≅ 936,35 [N]
| Fbx = Sx ≅ 253,35 [N]

(61)

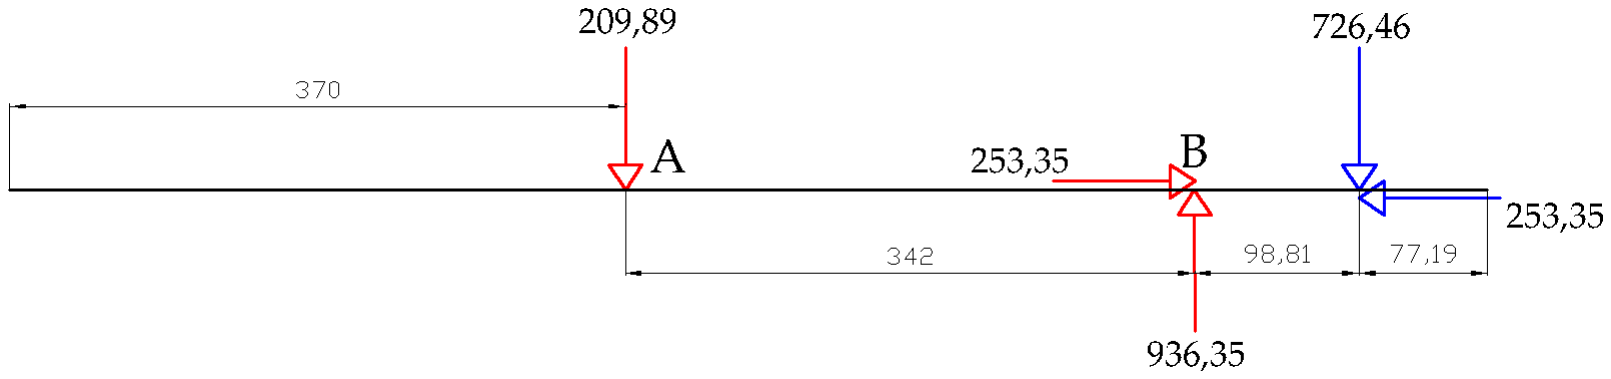
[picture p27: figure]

Figure 3-38 Axle shaft configuration - (Differential side).

The shear chart, the bending moment chart, the traction chart and the torque chart are subsequent:

Figure 3-39 Shear chart axle shaft - (Differential side).

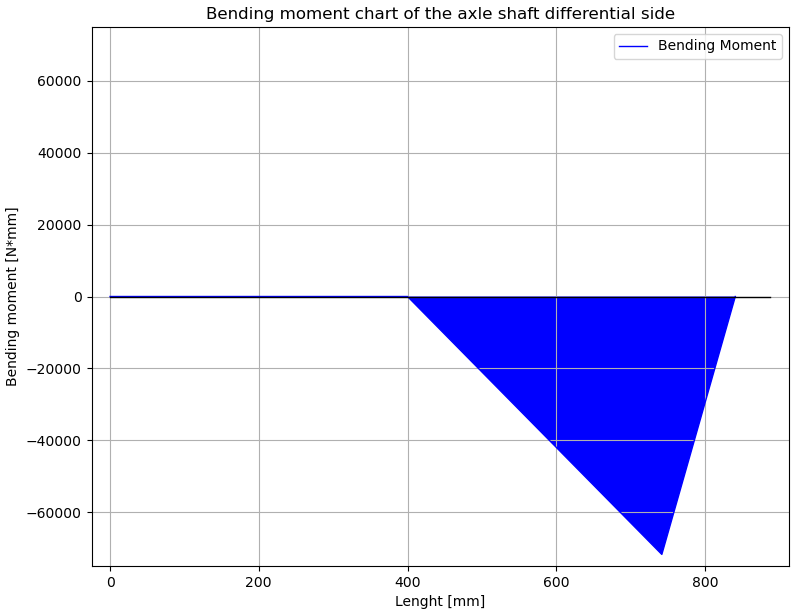
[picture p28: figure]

Figure 3-40 Bending moment chart axle shaft - (Differential side).

Figure 3-41 Traction chart axle shaft - (Differential side).

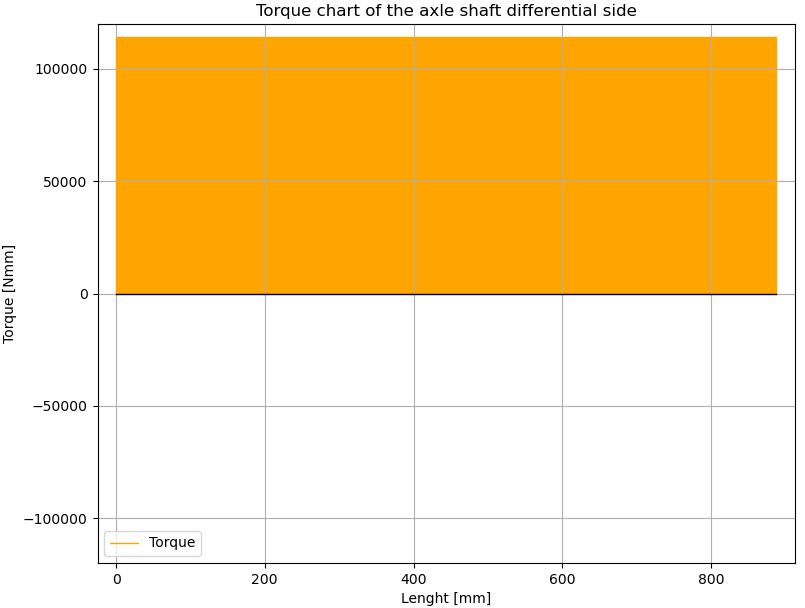
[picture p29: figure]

Figure 3-42 Torque chart axle shaft - (Differential side).
As already explained in the paragraphs 3.1.1.2 and 3.1.1.3, the ideal bending moment Mbi is evaluated with the following equivalence:

Mbi = √Mb
2 + 0,75 ∗ T

2 = √(209,89 ∗ 342)
2 + 0,75 ∗ 114000²

≅ 122063,86 [N ∗ mm]

(62)

Remembering that the minimum diameter is equal to:

d = √
32 ∗ Mbi

π ∗ σadm,f

3
(63)

Having σadm,f =

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
= 150 [MPa], where σU is the ultimate strength in MPa of the steel C60 and X is a safety factor, now d can be evaluated:

d = √
32 ∗ 122063,86
π ∗ 150

3
≅ 20,24 [mm]

(64)

About the bearings, there are not high loads applied to them and the maximum speed, calculated in the next equation, is not so high too:

naxle sℎaft =

nengine

iprimary reduction ∗ i6

tℎ ∗ idifferential

=

13000
1,8125 ∗ 0,5000 ∗ 3,5625 ≅ 4026,62 [rpm]

(65)

The bearing that needs to be installed in position B (Figure 3-37) in the real case is on the ring gear, check the next figure to better understand:

Figure 3-43 Ring Gear - Technical Drawing.

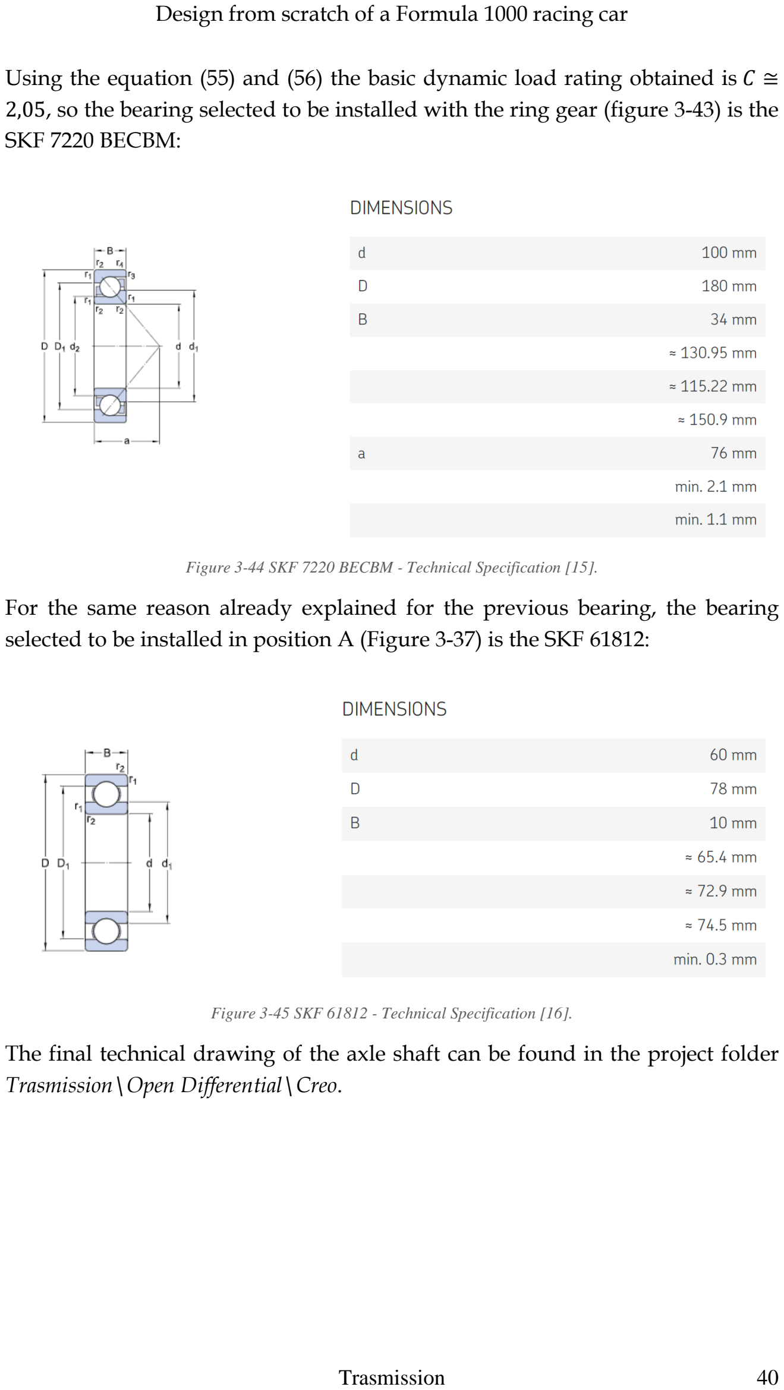
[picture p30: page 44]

Using the equation (55) and (56) the basic dynamic load rating obtained is C ≅ 2,05, so the bearing selected to be installed with the ring gear (figure 3-43) is the SKF 7220 BECBM:

Figure 3-44 SKF 7220 BECBM - Technical Specification [15].
For the same reason already explained for the previous bearing, the bearing selected to be installed in position A (Figure 3-37) is the SKF 61812:

Figure 3-45 SKF 61812 - Technical Specification [16].
The final technical drawing of the axle shaft can be found in the project folder Trasmission\Open Differential\Creo.

Suspensions | 41

## Overview

Figure 3-46 Differential overview.

## 4. Suspensions

Work in progress

Software | 42

## 5. Software

In this Chapter there is the description of each kind of software used in this thesis.

## CAE Software

## Altair® HyperWorks®

Altair® HyperWorks® is a computer-aided engineering (CAE) simulation software platform.
It consists all the modules of CAE i.e. modelling, meshing, solver. It is a complete package of finite element procedure. Preprocessing, Solving and Postprocessing can be done using Hyperworks.
HyperWorks is a product of that consisting of a number of software, the software used in this thesis are HyperMesh, HyperView and Inspire.

## 5.1.1.1 HyperMesh

It is part of the HyperWorks package, inside HM there are different Solvers as RADIOSS and OptiStruct, the last one is the solver used in this thesis. OptiStruct is a modern structural analysis solver for linear and nonlinear problems under static and dynamic loadings. It is the market-leading solution for structural design and optimization and it is based on finite-element and multi-body dynamics technology.

## 5.1.1.2 HyperView

It is a complete post-processing and visualization environment where is possible perform different studies, including finite element analysis and optimization. With ISO plots and element densities is possible to visualize and determine what geometry needs to be further post-processed.

Figure 5-1 Altair® logo

Software | 43

## Ansys®

Ansys develops and markets finite element analysis software used to simulate
engineering | problems. | The | software
creates simulated computer models of structures or machine components to simulate strength, toughness, elasticity and other attributes.
Most Ansys simulations are performed using the AW software.

## 5.1.2.1 Ansys® Workbench

It is a software environment to carry out various analyses such as structural, thermal and electromagnetic. It is structured in blocks and anyone of them is created to achieve different analysis in a diverse field.

## 5.1.2.2 SpaceClaim

It is integrated inside the Ansys software and is used to create, edit or repair geometries. Typically, it reads the STL files exported from Mechanical and do the post-process on the geometry before design validation. The geometry is then converted into a solid to analyse it again in ANSYS Mechanical.

## CAD Software

## Siemens® NX

It is a CAD/CAM/CAE software, in this thesis was used to perform the postprocessing on the geometries and to do the TO study since this feature with the last release of the software was implemented.

Figure 5-2 Ansys® logo

Figure 5-3 Siemens® NX logo

Software | 44

## SolidWorks®

SolidWorks is solid modelling software that allows you to design products in 3 dimensions. The technique is generally to sketch 2D profiles then use methods like extruding and lofting to produce the solid shape.

Figure 5-4 Solidworks® logo

## PTC Creo®

Creo is a family or suite of Computer-aided design (CAD) apps supporting product design for discrete manufacturers and is developed by PTC. The suite consists of apps, each delivering a distinct set of capabilities for a user role within product development.
Creo provides apps for 3D CAD parametric feature solid modeling, 3D direct modeling, 2D orthographic views, Finite Element Analysis and simulation, schematic design, technical illustrations, and viewing and visualization.

Figure 5-5 PTC Creo® logo

## Catia V5

CATIA software (an acronym of computer-aided three-dimensional interactive application) is a multi-platform software suite for computer-aided design (CAD), computer-aided manufacturing (CAM), computer-aided engineering (CAE), PLM and 3D, developed by the French company Dassault Systèmes.

Figure 5-6 Catia® V5 logo

Software | 45

## Mathematical Solvers

## MATLAB®

MATLAB (matrix laboratory) is a multi-paradigm numerical computing environment and proprietary programming language developed by MathWorks. MATLAB allows matrix manipulations, plotting of functions and data, implementation of algorithms, creation of user interfaces, and interfacing with programs written in other languages.

## PyCharm®

PyCharm® is an integrated development environment (IDE) used in computer programming, specifically for the Python language. It is developed by the Czech company JetBrains. It provides code analysis, a graphical debugger, an integrated unit tester, integration with version control systems (VCSes), and supports web development with Django as well as Data Science with Anaconda.

Figure 5-7 MATLAB® logo

Figure 5-8 PyCharm® logo

List of Figures | 46

## List of Figures

Figure 3-3 Example of 1

Figure 3-8 Layshaft 1
Figure 3-9 Layshaft 1
Figure 3-10 Shear chart 1
Figure 3-11 Bending moment chart 1 Figure 3-12 Torque chart 1

Figure 3-18 Mainshaft 1
Figure 3-19 Mainshaft 1
Figure 3-20 Shear chart 1
Figure 3-21 Bending moment chart 1 Figure 3-22 Traction chart 1
Figure 3-23 Torque chart 1

Figure 3-29 Disk 1

st
- 2

nd

47

## References

[1] “Formula 1000 Technical Regulations – Version 1,” [Online]. Available: http://frca.net.au/wp-content/uploads/2013_Formula_1000_Technical_Regulations_-_Version_1.pdf. [Accessed June 2020].
[2] “THE NEED FOR SPEED,” [Online]. Available: https://heraldonlinejournal.com/2020/01/17/the-need-for-speed/. [Accessed June 2020].
[3] “2014 CBR1000RR Aftermarket Exhaust and Dyno Tuning,” [Online]. Available: http://superbikesolutions.blogspot.com/2015/08/2014-cbr1000rr-aftermarket-exhaust-and.html. [Accessed June 2020].
[4] “CBR1000RR,” Honda, [Online]. Available: https://www.motorcyclespecs.co.za/model/Honda/honda_cbr1000rr_sp_14.html. [Accessed June 2020].
[5] D. Seward, Race Car Design, Palgrave, 2014.
[6] “F1 transmission system explained,” 13 February 2015. [Online]. Available: https://www.sportskeeda.com/f1/f1-transmission-system-explained. [Accessed June 2020].
[7] L. Caligaris, S. Fava e C. Tomasello, Manuale di Meccanica, Hoepli Milano, 2011.
[8] “Standard Metric Keys & Keyways,” [Online]. Available: http://www.jaredzone.info/2010/12/standard-metric-keys-keyways.html. [Accessed July 2020].
[9] “62/22,” SKF, [Online]. Available: https://www.skf.com/group/products/rolling-bearings/ball-bearings/deep-groove-ball-bearings/productid-62%2F22. [Accessed July 2020].
[10] O. Chandler, “Gears and Cams,” [Online]. Available: https://slideplayer.com/slide/13238058/. [Accessed July 2020].
[11] “Straight-sided splines for cylindrical shafts with internal centering - Dimensions, tolerances and verification,” [Online]. Available: https://www.saiglobal.com/PDFTemp/Previews/OSH/ISO/ISO_12345_07-01/T003596E.PDF. [Accessed June 2020].
[12] “320/22 X,” SKF, [Online]. Available: https://www.skf.com/group/products/rolling-bearings/roller-bearings/tapered-roller-bearings/single-row-tapered-roller-bearings/productid-320%2F22%20X. [Accessed July 2020].
[13] “RNAO45X62X40-ZW-ASR1-XL,” Schaeffler, [Online]. Available: https://medias.schaeffler.com/medias/it!hp.ec.br.pr/RNAO..-ZW-ASR1*RNAO45X62X40-ZW-ASR1-XL;bvhRp4WWpLlc?lang=en. [Accessed July 2020].
[14] “61809-Y,” Schaeffler, [Online]. Available: https://medias.schaeffler.com/medias/en!hp.ec.br.pr/618*61809-Y?clrsb=1&. [Accessed July 2020].
[15] “7220 BECBM,” SKF, [Online]. Available: https://www.skf.com/us/products/rolling-bearings/ball-bearings/angular-contact-

References | 48

ball-bearings/single-row-angular-contact-ball-bearings/productid-7220%20BECBM. [Accessed July 2020].
[16] “61812,” SKF, [Online]. Available: https://www.skf.com/sg/products/rolling-bearings/ball-bearings/deep-groove-ball-bearings/productid-61812. [Accessed July 2020].
[17] “SMA4-25,” KHK, [Online]. Available: https://khkgears2.net/catalog6/SMA4-25. [Accessed July 2020].

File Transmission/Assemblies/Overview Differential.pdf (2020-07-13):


7220 BECBM

Ring Gear

SKF

Spider Gear

Spider Gear

Side Gear
Side Gear

Pinion Shaft

Axle Shaft

Axle Shaft

SKF 61812

7220 BECBM

Ring Gear

SKF

Spider Gear

Spider Gear

Side Gear
Side Gear

Pinion Shaft

Axle Shaft

Axle Shaft

SKF 61812

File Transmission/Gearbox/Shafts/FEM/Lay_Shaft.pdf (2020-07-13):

# Lay_Shaft*

First Saved | Monday, June 29, 2020
Last Saved | Wednesday, July 1, 2020
Product Version | 2020 R1
Save Project Before Solution | No
Save Project After Solution | No
Lay_Shaft* | Page 1 of 20


file:///C:/Users/marin/AppData/Roaming/Ansys/v201/Mechanical_Report/Mechanical... 01/07/2020

# Contents

l Units

l Model (B4)
¡ Geometry
n Geom\LAY_SHAFT
¡ Materials
¡ Coordinate Systems
¡ Mesh
n Mesh Controls
¡ Named Selections
¡ Static Structural (B5)
n Analysis Settings
n Loads
n Solution (B6)
n Solution Information
n Results

l Material Data
¡ Steel C60

# Units

TABLE 1

# Model (B4)

Unit System | Metric (mm, kg, N, s, mV, mA) Degrees rad/s Celsius
Angle | Degrees
Rotational Velocity | rad/s
Temperature | Celsius

## Geometry

TABLE 2
Model (B4) > Geometry
Object Name | Geometry
State | Fully Defined
Definition
Source | D:\Google Drive\Progetti\Formula 1000\Trasmission\FEM\Shafts\Lay_Shaft_files\dp0\Geom\DM\Geom.scdoc
Type | SpaceClaim
Length Unit | Meters
Element Control | Program Controlled
Display Style | Body Color
Bounding Box
Length X | 40, mm
Length Y | 40, mm
Length Z | 850, mm
Properties
Volume | 9,476e+005 mm³
Mass | 7,3913 kg
Scale Factor Value | 1,
Statistics
Bodies | 1
Active Bodies | 1
Nodes | 28036
Elements | 17377
Mesh Metric | None
Update Options
Assign Default Material | No
Basic Geometry Options
Solid Bodies | Yes
Surface Bodies | Yes
Line Bodies | Yes
Parameters | Independent
Parameter Key
Attributes | Yes
Attribute Key
Named Selections | Yes
Named Selection Key
Material Properties | Yes
Advanced Geometry Options
Use Associativity | Yes
Coordinate Systems | Yes
Coordinate System Key
Reader Mode Saves Updated File | No
Use Instances | Yes
Smart CAD Update | Yes
Compare Parts On Update | No
Lay_Shaft* | Page 2 of 20

TABLE 3
Model (B4) > Geometry > Parts

TABLE 4
Model (B4) > Materials
Analysis Type | 3-D
Mixed Import Resolution | None
Clean Bodies On Import | No
Stitch Surfaces On Import | None
Decompose Disjoint Geometry | Yes
Enclosure and Symmetry Processing | Yes
Object Name | Geom\LAY_SHAFT
State | Meshed
Graphics Properties
Visible | Yes
Transparency | 1
Definition
Suppressed | No
Stiffness Behavior | Flexible
Coordinate System | Default Coordinate System
Reference Temperature | By Environment
Treatment | None
Material
Assignment | Steel C60
Nonlinear Effects | Yes
Thermal Strain Effects | Yes
Bounding Box
Length X | 40, mm
Length Y | 40, mm
Length Z | 850, mm
Properties
Volume | 9,476e+005 mm³
Mass | 7,3913 kg
Centroid X | -0,39801 mm
Centroid Y | -1,5049e-005 mm
Centroid Z | 349,71 mm
Moment of Inertia Ip1 | 3,7241e+005 kg·mm²
Moment of Inertia Ip2 | 3,7236e+005 kg·mm²
Moment of Inertia Ip3 | 1380,6 kg·mm²
Statistics
Nodes | 28036
Elements | 17377
Mesh Metric | None
CAD Attributes
PartTolerance: | 0,00000001
Color:175.143.175
Object Name | Materials
State | Fully Defined
Statistics
Materials | 2
Material Assignments | 0

## Coordinate Systems

TABLE 5
Model (B4) > Coordinate Systems > Coordinate System
Object Name | Global Coordinate System
State | Fully Defined
Definition
Type | Cartesian
Coordinate System ID | 0,
Origin
Origin X | 0, mm
Origin Y | 0, mm
Origin Z | 0, mm
Directional Vectors
X Axis Data | [ 1, 0, 0, ]
Y Axis Data | [ 0, 1, 0, ]
Z Axis Data | [ 0, 0, 1, ]

## Mesh

TABLE 6
Model (B4) > Mesh
Object Name | Mesh
State | Solved
Display
Display Style Use Geometry Setting Defaults
Physics Preference | Mechanical
Element Order | Program Controlled
Lay_Shaft* | Page 3 of 20

TABLE 7
Model (B4) > Mesh > Mesh Controls
Element Size | Default
Sizing
Use Adaptive Sizing | Yes
Resolution | Default (2)
Mesh Defeaturing | Yes
Defeature Size | Default
Transition | Fast
Span Angle Center | Coarse
Initial Size Seed | Assembly
Bounding Box Diagonal | 851,88 mm
Average Surface Area | 1207, mm²
Minimum Edge Length | 1,971 mm
Quality
Check Mesh Quality | Yes, Errors
Error Limits | Aggressive Mechanical
Target Quality | Default (0.050000)
Smoothing | Medium
Mesh Metric | None
Inflation
Use Automatic Inflation | None
Inflation Option | Smooth Transition
Transition Ratio | 0,272
Maximum Layers | 5
Growth Rate | 1,2
Inflation Algorithm | Pre
View Advanced Options | No
Advanced
Number of CPUs for Parallel Part Meshing | Program Controlled
Straight Sided Elements | No
Rigid Body Behavior | Dimensionally Reduced
Triangle Surface Mesher | Program Controlled
Topology Checking | Yes
Pinch Tolerance | Please Define
Generate Pinch on Refresh | No
Statistics
Nodes | 28036
Elements | 17377
Object Name | Automatic Method | Body Sizing
State | Fully Defined
Scope
Scoping Method | Geometry Selection
Geometry | 1 Body
Definition
Suppressed | No
Method | Automatic
Element Order | Use Global Setting
Type | | Element Size
Element Size | | 8, mm
Advanced
Defeature Size | Default
Behavior | Soft

## Named Selections

TABLE 8
Model (B4) > Named Selections > Named Selections

# Static Structural (B5)

TABLE 9
Model (B4) > Analysis
Object Name | Bearing A | Bearing B | Gear 3 | Gear 1 | Gear 4 | Gear 5 | Gear 6 | Gear 2 | Input
State | Fully Defined
Scope
Scoping Method | Geometry Selection
Geometry | 2 Faces | 1 Face | 2 Faces
Definition
Send to Solver | Yes
Protected | Program Controlled
Visible | Yes
Program Controlled Inflation | Exclude
Preserve During Solve (Beta) | No
Statistics
Type | Manual
Total Selection | 2 Faces | 1 Face | 2 Faces
Surface Area | 966,38 mm² | 966,39 mm² | 600, mm²
Suppressed | 0
Used by Mesh Worksheet | No
Lay_Shaft* | Page 4 of 20

TABLE 10
Model (B4) > Static Structural (B5) > Analysis Settings

TABLE 11
Model (B4) > Static Structural (B5) > Analysis Settings Step-Specific "Step Controls"

TABLE 12
Model (B4) > Static Structural (B5) > Loads
Object Name | Static Structural (B5)
State | Solved
Definition
Physics Type | Structural
Analysis Type | Static Structural
Solver Target | Mechanical APDL
Options
Environment Temperature | 22, °C
Generate Input Only | No
Object Name | Analysis Settings
State | Fully Defined
Step Controls
Number Of Steps | 6,
Current Step Number | 6,
Step End Time | 6, s
Auto Time Stepping | Program Controlled
Solver Controls
Solver Type | Program Controlled
Weak Springs | Off
Solver Pivot Checking | Program Controlled
Large Deflection | Off
Inertia Relief | Off
Rotordynamics Controls
Coriolis Effect | Off
Restart Controls
Generate Restart Points | Program Controlled
Retain Files After Full Solve | No
Combine Restart Files | Program Controlled
Nonlinear Controls
Newton-Raphson Option | Program Controlled
Force Convergence | Program Controlled
Moment Convergence | Program Controlled
Displacement Convergence | Program Controlled
Rotation Convergence | Program Controlled
Line Search | Program Controlled
Stabilization | Program Controlled
Advanced
Inverse Option | No
Contact Split (DMP) | Off
Output Controls
Stress | Yes
Surface Stress | No
Back Stress | No
Strain | Yes
Contact Data | Yes
Nonlinear Data | No
Nodal Forces | No
Volume and Energy | Yes
Euler Angles | Yes
Contact Miscellaneous | No
General Miscellaneous | No
Store Results At | All Time Points
Result File Compression | Program Controlled
Analysis Data Management
Solver Files Directory | D:\Google Drive\Progetti\Formula 1000\Trasmission\FEM\Shafts\Lay_Shaft_files\dp0\SYS\MECH\
Future Analysis | None
Scratch Solver Files Directory
Save MAPDL db | No
Contact Summary | Program Controlled
Delete Unneeded Files | Yes
Nonlinear Solution | No
Solver Units | Active System
Solver Unit System | nmm
Step | Step End Time
1 1, s
2 2, s
3 3, s
4 4, s
5 5, s
6 6, s
Object Name | Input | Gear 1 | Gear 2 | Gear 3 | Gear 4 | Gear 5 | Gear 6 | Bearing A | Bearing B | Input | Gear 1
State | Fully Defined
Lay_Shaft* | Page 5 of 20

FIGURE 1
Model (B4) > Static Structural (B5) > Input


TABLE 13
Model (B4) > Static Structural (B5) > Input

FIGURE 2
Model (B4) > Static Structural (B5) > Gear 1


TABLE 14
Model (B4) > Static Structural (B5) > Gear 1

Scope
Scoping Method | Named Selection | Geometry Selection
Named Selection | Input | Gear 1 | Gear 2 | Gear 3 | Gear 4 | Gear 5 | Gear 6 | Bearing A | Bearing B
Geometry | | | | | | | | | | 4 Edges
Definition
Type | Force | Fixed Support | Moment
Define By | Vector | | Vector
Applied By | Surface Effect
Magnitude | Tabular Data | | Tabular Data
Direction | Defined | | Defined
Suppressed | No
Behavior | | | Deformable
Tabular Data
Independent Variable | Time | Time
Advanced
Pinball Region | | All
Steps | Time [s] | Force [N]
1 | 0, | 0,
| 1, | 1673,3
2 2,
3 3,
4 4,
5 5,
6 6,
Lay_Shaft* | Page 6 of 20

FIGURE 3
Model (B4) > Static Structural (B5) > Gear 2


TABLE 15
Model (B4) > Static Structural (B5) > Gear 2

FIGURE 4
Model (B4) > Static Structural (B5) > Gear 3


TABLE 16
Model (B4) > Static Structural (B5) > Gear 3
Steps | Time [s] | Force [N]
1 | 0, | 0,
| 1, | -3235,1
2 2, | | 0,
3 3,
4 4,
5 5,
6 6,
Steps | Time [s] | Force [N]
1 | 0, | 0, 1,
2 | 2, | -2426,3
3 3,
| 4, | 0, 4
5 5,
6 6,
Steps | Time [s] | Force [N]
1 | 0,
| 1, | 0,
2 2,
3 | 3, | -1797,3
4 4, | | 0,
5 | 5,
6 6,
Lay_Shaft* | Page 7 of 20

FIGURE 5
Model (B4) > Static Structural (B5) > Gear 4


TABLE 17
Model (B4) > Static Structural (B5) > Gear 4

FIGURE 6
Model (B4) > Static Structural (B5) > Gear 5


TABLE 18
Model (B4) > Static Structural (B5) > Gear 5

FIGURE 7
Model (B4) > Static Structural (B5) > Gear 6
Steps | Time [s] | Force [N]
1 | 0,
0, 1,
2 2,
3 3,
4 | 4, | -1617,5
5 | 5, 6, | 0, 6
Steps | Time [s] | Force [N]
1 | 0, | 0,
1,
2 2,
3 3,
4 4,
5 | 5, | -1516,5
6 | 6, | 0,
Lay_Shaft* | Page 8 of 20

TABLE 19
Model (B4) > Static Structural (B5) > Gear 6

FIGURE 8
Model (B4) > Static Structural (B5) > Input


TABLE 20
Model (B4) > Static Structural (B5) > Input

FIGURE 9
Model (B4) > Static Structural (B5) > Gear 1
Steps | Time [s] | Force [N]
1 | 0, | 0,
1,
2 2,
3 3,
4 4,
5 5,
6 | 6, | -1427,3
Steps | Time [s] | Moment [N·mm]
1 | 0, | 0,
| 1, | 1,14e+005
2 2,
3 3,
4 4,
5 5,
6 6,
Lay_Shaft* | Page 9 of 20


TABLE 21
Model (B4) > Static Structural (B5) > Gear 1

TABLE 22
Model (B4) > Static Structural (B5) > Loads

FIGURE 10
Model (B4) > Static Structural (B5) > Gear 2


TABLE 23
Model (B4) > Static Structural (B5) > Gear 2
Steps | Time [s] | Moment [N·mm]
1 | 0, | 0,
| 1, | 1,14e+005
2 2, | | 0,
3 3,
4 4,
5 5,
6 6,
Object Name | Gear 2 | Gear 3 | Gear 4 | Gear 5 | Gear 6
State | Fully Defined
Scope
Scoping Method | Geometry Selection
Geometry | 4 Edges | 6 Edges | 4 Edges
Definition
Type | Moment
Define By | Vector
Magnitude | Tabular Data
Direction | Defined
Suppressed | No
Behavior | Deformable
Tabular Data
Independent Variable | Time
Advanced
Pinball Region | All
Lay_Shaft* | Page 10 of 20

FIGURE 11
Model (B4) > Static Structural (B5) > Gear 3


TABLE 24
Model (B4) > Static Structural (B5) > Gear 3

FIGURE 12
Model (B4) > Static Structural (B5) > Gear 4


TABLE 25
Model (B4) > Static Structural (B5) > Gear 4
Steps | Time [s] | Moment [N·mm]
1 | 0, | 0, 1,
2 | 2, | 1,14e+005
3 3,
| 4, | 0, 4
5 5,
6 6,
Steps | Time [s] | Moment [N·mm]
1 | 0,
| 1, | 0,
2 2,
3 | 3, | 1,14e+005
4 4, | | 0,
5 | 5,
6 6,
Steps | Time [s] | Moment [N·mm]
1 | 0, | 0, 1,

2 2,
3 3,
4 | 4, | 1,14e+005
5 | 5, 6, | 0, 6
Lay_Shaft* | Page 11 of 20

FIGURE 13
Model (B4) > Static Structural (B5) > Gear 5


TABLE 26
Model (B4) > Static Structural (B5) > Gear 5

FIGURE 14
Model (B4) > Static Structural (B5) > Gear 6


TABLE 27
Model (B4) > Static Structural (B5) > Gear 6
Steps | Time [s] | Moment [N·mm]
1 | 0, | 0,
1,
2 2,
3 3,
4 4,
5 | 5, | 1,14e+005
6 | 6, | 0,
Steps | Time [s] | Moment [N·mm]
1 | 0, | 0,
1,
2 2,
3 3,
4 4,
5 5,
6 | 6, | 1,14e+005

## Solution (B6)

TABLE 28
Model (B4) > Static Structural (B5) > Solution
Object Name | Solution (B6)
State | Solved
Adaptive Mesh Refinement
Max Refinement Loops | 1,
Lay_Shaft* | Page 12 of 20

TABLE 29
Model (B4) > Static Structural (B5) > Solution (B6) > Solution Information

TABLE 30
Model (B4) > Static Structural (B5) > Solution (B6) > Results

FIGURE 15
Model (B4) > Static Structural (B5) > Solution (B6) > Equivalent Stress 1

Refinement Depth 2,
Information
Status | Done
MAPDL Elapsed Time | 29, s
MAPDL Memory Used | 210, MB
MAPDL Result File Size | 47,75 MB
Post Processing
Beam Section Results | No
On Demand Stress/Strain | No
Object Name | Solution Information
State | Solved
Solution Information
Solution Output | Solver Output
Newton-Raphson Residuals | 0
Identify Element Violations | 0
Update Interval | 2,5 s
Display Points | All
FE Connection Visibility
Activate Visibility | Yes
Display | All FE Connectors
Draw Connections Attached To | All Nodes
Line Color | Connection Type
Visible on Results | No
Line Thickness | Single
Display Type | Lines
Object Name | Equivalent Stress 1 | Equivalent Stress 2 | Equivalent Stress 3 | Equivalent Stress 4 | Equivalent Stress 5 | Equivalent Stress 6 | Total Deformation | Total Deformation 2 | Total Deformation 3 | Total Deformation 4 | Total Deformation 5
State | Solved
Scope
Scoping Method | Geometry Selection
Geometry | All Bodies
Definition
Type | Equivalent (von-Mises) Stress | Total Deformation
By | Time
Display Time | 1, s | 2, s | 3, s | 4, s | 5, s | 6, s | 1, s | 2, s | 3, s | 4, s | 5, s
Calculate Time History | Yes

Identifier
Suppressed | No
Integration Point Results
Display Option | Averaged
Average Across Bodies | No

Results
Minimum | 2,0499e-003 MPa | 5,3872e-004 MPa | 1,1958e-003 MPa | 3,3569e-004 MPa | 3,8914e-004 MPa | 7,0659e-004 MPa | 0, mm
Maximum | 170,01 MPa | 71,598 MPa | 78,666 MPa | 117,48 MPa | 111,77 MPa | 83,335 MPa | 0,45402 mm | 0,15047 mm | 3,3492e-002 mm | 0,16973 mm | 0,19104 mm
Average | 15,882 MPa | 6,3235 MPa | 6,7477 MPa | 9,4638 MPa | 9,6688 MPa | 9,0242 MPa | 0,22602 mm | 7,7233e-002 mm | 1,4362e-002 mm | 7,5638e-002 mm | 8,5582e-002 mm
Minimum Occurs On | Geom\LAY_SHAFT
Maximum Occurs On | Geom\LAY_SHAFT

Minimum Value Over Time
Minimum | 3,3569e-004 MPa | 0, mm
Maximum | 2,0499e-003 MPa | 0, mm
Maximum Value Over Time
Minimum | 71,598 MPa | 3,3492e-002 mm
Maximum | 170,01 MPa | 0,45402 mm
Information
Time | 1, s | 2, s | 3, s | 4, s | 5, s | 6, s | 1, s | 2, s | 3, s | 4, s | 5, s
Load Step | 1 | 2 | 3 | 4 | 5 | 6 | 1 | 2 | 3 | 4 | 5
Substep | 1
Iteration Number | 1 | 2 | 3 | 4 | 5 | 6 | 1 | 2 | 3 | 4 | 5
Lay_Shaft* | Page 13 of 20


TABLE 31
Model (B4) > Static Structural (B5) > Solution (B6) > Equivalent Stress 1

FIGURE 16
Model (B4) > Static Structural (B5) > Solution (B6) > Equivalent Stress 2


TABLE 32
Model (B4) > Static Structural (B5) > Solution (B6) > Equivalent Stress 2

FIGURE 17
Model (B4) > Static Structural (B5) > Solution (B6) > Equivalent Stress 3
Time [s] | Minimum [MPa] | Maximum [MPa] | Average [MPa]
1, | 2,0499e-003 | 170,01 | 15,882
2, | 5,3872e-004 | 71,598 | 6,3235
3, | 1,1958e-003 | 78,666 | 6,7477
4, | 3,3569e-004 | 117,48 | 9,4638
5, | 3,8914e-004 | 111,77 | 9,6688
6, | 7,0659e-004 | 83,335 | 9,0242
Time [s] | Minimum [MPa] | Maximum [MPa] | Average [MPa]
1, | 2,0499e-003 | 170,01 | 15,882
2, | 5,3872e-004 | 71,598 | 6,3235
3, | 1,1958e-003 | 78,666 | 6,7477
4, | 3,3569e-004 | 117,48 | 9,4638
5, | 3,8914e-004 | 111,77 | 9,6688
6, | 7,0659e-004 | 83,335 | 9,0242
Lay_Shaft* | Page 14 of 20

TABLE 33
Model (B4) > Static Structural (B5) > Solution (B6) > Equivalent Stress 3

FIGURE 18
Model (B4) > Static Structural (B5) > Solution (B6) > Equivalent Stress 4


TABLE 34
Model (B4) > Static Structural (B5) > Solution (B6) > Equivalent Stress 4

FIGURE 19
Model (B4) > Static Structural (B5) > Solution (B6) > Equivalent Stress 5
Time [s] | Minimum [MPa] | Maximum [MPa] | Average [MPa]
1, | 2,0499e-003 | 170,01 | 15,882
2, | 5,3872e-004 | 71,598 | 6,3235
3, | 1,1958e-003 | 78,666 | 6,7477
4, | 3,3569e-004 | 117,48 | 9,4638
5, | 3,8914e-004 | 111,77 | 9,6688
6, | 7,0659e-004 | 83,335 | 9,0242
Time [s] | Minimum [MPa] | Maximum [MPa] | Average [MPa]
1, | 2,0499e-003 | 170,01 | 15,882
2, | 5,3872e-004 | 71,598 | 6,3235
3, | 1,1958e-003 | 78,666 | 6,7477
4, | 3,3569e-004 | 117,48 | 9,4638
5, | 3,8914e-004 | 111,77 | 9,6688
6, | 7,0659e-004 | 83,335 | 9,0242
Lay_Shaft* | Page 15 of 20


TABLE 35
Model (B4) > Static Structural (B5) > Solution (B6) > Equivalent Stress 5

FIGURE 20
Model (B4) > Static Structural (B5) > Solution (B6) > Equivalent Stress 6


TABLE 36
Model (B4) > Static Structural (B5) > Solution (B6) > Equivalent Stress 6

FIGURE 21
Model (B4) > Static Structural (B5) > Solution (B6) > Total Deformation
Time [s] | Minimum [MPa] | Maximum [MPa] | Average [MPa]
1, | 2,0499e-003 | 170,01 | 15,882
2, | 5,3872e-004 | 71,598 | 6,3235
3, | 1,1958e-003 | 78,666 | 6,7477
4, | 3,3569e-004 | 117,48 | 9,4638
5, | 3,8914e-004 | 111,77 | 9,6688
6, | 7,0659e-004 | 83,335 | 9,0242
Time [s] | Minimum [MPa] | Maximum [MPa] | Average [MPa]
1, | 2,0499e-003 | 170,01 | 15,882
2, | 5,3872e-004 | 71,598 | 6,3235
3, | 1,1958e-003 | 78,666 | 6,7477
4, | 3,3569e-004 | 117,48 | 9,4638
5, | 3,8914e-004 | 111,77 | 9,6688
6, | 7,0659e-004 | 83,335 | 9,0242
Lay_Shaft* | Page 16 of 20


TABLE 37
Model (B4) > Static Structural (B5) > Solution (B6) > Total Deformation

FIGURE 22
Model (B4) > Static Structural (B5) > Solution (B6) > Total Deformation 2


TABLE 38
Model (B4) > Static Structural (B5) > Solution (B6) > Total Deformation 2

FIGURE 23
Model (B4) > Static Structural (B5) > Solution (B6) > Total Deformation 3
Time [s] | Minimum [mm] | Maximum [mm] | Average [mm]
1, | 0, | 0,45402 | 0,22602
2, | | 0,15047 | 7,7233e-002
3, | | 3,3492e-002 | 1,4362e-002
4, | | 0,16973 | 7,5638e-002
5, | | 0,19104 | 8,5582e-002
6, | | 0,20324 | 9,3101e-002
Time [s] | Minimum [mm] | Maximum [mm] | Average [mm]
1, | 0, | 0,45402 | 0,22602
2, | | 0,15047 | 7,7233e-002
3, | | 3,3492e-002 | 1,4362e-002
4, | | 0,16973 | 7,5638e-002
5, | | 0,19104 | 8,5582e-002
6, | | 0,20324 | 9,3101e-002
Lay_Shaft* | Page 17 of 20


TABLE 39
Model (B4) > Static Structural (B5) > Solution (B6) > Total Deformation 3

FIGURE 24
Model (B4) > Static Structural (B5) > Solution (B6) > Total Deformation 4


TABLE 40
Model (B4) > Static Structural (B5) > Solution (B6) > Total Deformation 4

FIGURE 25
Model (B4) > Static Structural (B5) > Solution (B6) > Total Deformation 5
Time [s] | Minimum [mm] | Maximum [mm] | Average [mm]
1, | 0, | 0,45402 | 0,22602
2, | | 0,15047 | 7,7233e-002
3, | | 3,3492e-002 | 1,4362e-002
4, | | 0,16973 | 7,5638e-002
5, | | 0,19104 | 8,5582e-002
6, | | 0,20324 | 9,3101e-002
Time [s] | Minimum [mm] | Maximum [mm] | Average [mm]
1, | 0, | 0,45402 | 0,22602
2, | | 0,15047 | 7,7233e-002
3, | | 3,3492e-002 | 1,4362e-002
4, | | 0,16973 | 7,5638e-002
5, | | 0,19104 | 8,5582e-002
6, | | 0,20324 | 9,3101e-002
Lay_Shaft* | Page 18 of 20

TABLE 41
Model (B4) > Static Structural (B5) > Solution (B6) > Total Deformation 5

TABLE 42
Model (B4) > Static Structural (B5) > Solution (B6) > Results

FIGURE 26
Model (B4) > Static Structural (B5) > Solution (B6) > Total Deformation 6
Time [s] | Minimum [mm] | Maximum [mm] | Average [mm]
1, | 0, | 0,45402 | 0,22602
2, | | 0,15047 | 7,7233e-002
3, | | 3,3492e-002 | 1,4362e-002
4, | | 0,16973 | 7,5638e-002
5, | | 0,19104 | 8,5582e-002
6, | | 0,20324 | 9,3101e-002
Object Name | Total Deformation 6
State | Solved
Scope
Scoping Method | Geometry Selection
Geometry | All Bodies
Definition
Type | Total Deformation
By | Time
Display Time | 6, s
Calculate Time History | Yes
Identifier
Suppressed | No
Results
Minimum | 0, mm
Maximum | 0,20324 mm
Average | 9,3101e-002 mm
Minimum Occurs On | Geom\LAY_SHAFT
Maximum Occurs On | Geom\LAY_SHAFT
Minimum Value Over Time
Minimum | 0, mm
Maximum | 0, mm
Maximum Value Over Time
Minimum | 3,3492e-002 mm
Maximum | 0,45402 mm
Information
Time | 6, s
Load Step | 6
Substep | 1
Iteration Number | 6
Lay_Shaft* | Page 19 of 20


TABLE 43
Model (B4) > Static Structural (B5) > Solution (B6) > Total Deformation 6

# Material Data

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

## Steel C60

TABLE 44
Steel C60 > Constants

TABLE 45
Steel C60 > Color

TABLE 46
Steel C60 > Isotropic Elasticity

TABLE 47
Steel C60 > Tensile Yield Strength

TABLE 48
Steel C60 > Tensile Ultimate Strength

TABLE 49
Steel C60 > Melting Temperature
Coefficient of Thermal Expansion | 1,08e-005 C^-1
Density | 7,8e-006 kg mm^-3
Red | Green | Blue
170, | 170, | 170,
Young's Modulus MPa | Poisson's Ratio | Bulk Modulus MPa | Shear Modulus MPa | Temperature C
2,17e+005 | 0,29 | 1,7222e+005 | 84109

Tensile Yield Strength MPa 620,

Tensile Ultimate Strength MPa 900,

Melting Temperature C
1350,
Lay_Shaft* | Page 20 of 20

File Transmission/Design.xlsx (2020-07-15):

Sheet: Engine
Engine | CBR1000RR | 2018 | https://www.hondabigwing.in/cbr1000rr | Weight Car | 4806.9 | N | Done in python
 |  |  |  | Wheelbase | 3250 | mm
Type | Liquid-cooled 4-stroke 16-valve DOHC Inline-4 |  |  | Static rear axle load | 2643.80 | N
Engine Displacement (cc) | 999 |  |  | Static front axle load | 2163.11 | N
No. of Valves per Cylinder | 4 |  |  | height center mass | 325 | mm
Bore Stroke (mm) | 76 | 55.1 |  | average coefficient of friction | 1.2
Compression Ratio | 13 | ±0.2:01 |  | Traction force | 3605.18 | N
Max. Power Output (kW) | 141 | at 13000 rpm |  | Longitudinal load transfer | 360.52 | N
Max. Torque (Nm) | 114 | at 11000 rpm |  | Rear wheel loads | 1502.16 | N
Oil Capacity (L) | 3.4 |  |  | Front wheel loads | 901.29 | N
 |  |  |  | diameter wheel (m) | 0.3302 | m
 |  |  |  | Peak torque rear wheels | 1190.43 | Nm
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

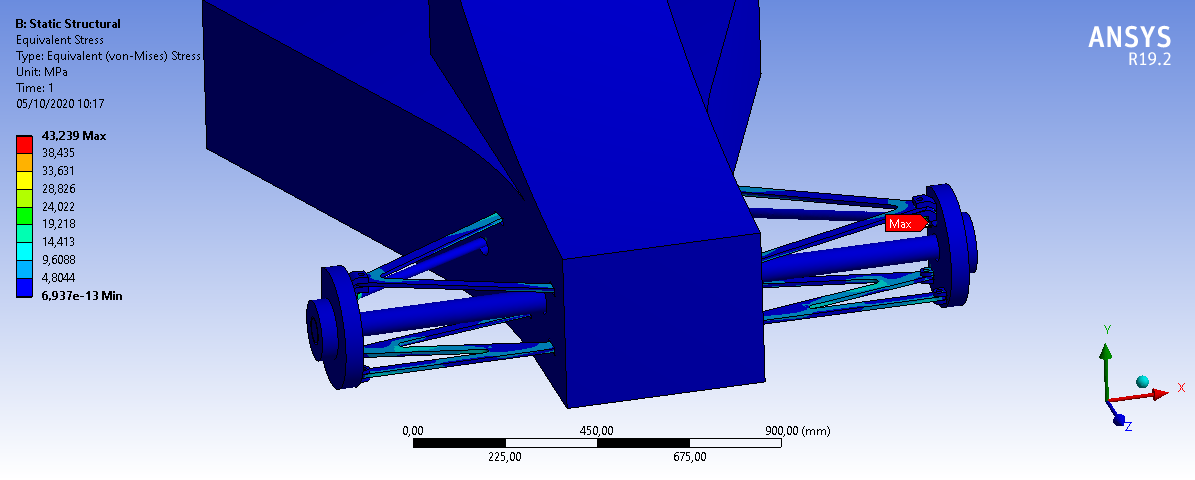
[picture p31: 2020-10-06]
Suspensions/Python/Plots/Rear_stress.png

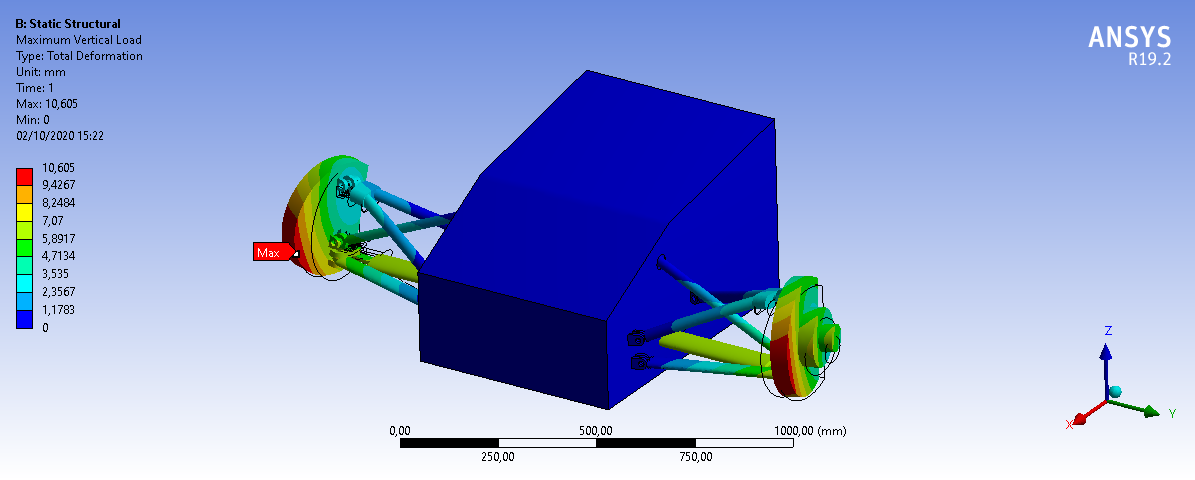
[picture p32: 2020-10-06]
Suspensions/Python/Plots/MVL_def.png

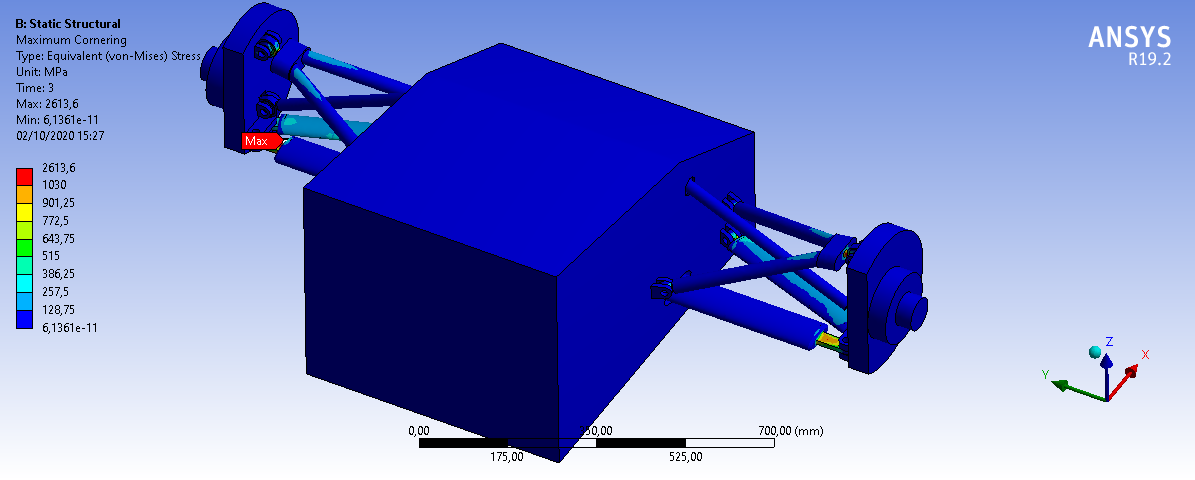
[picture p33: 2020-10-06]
Suspensions/Python/Plots/MC_stress.png

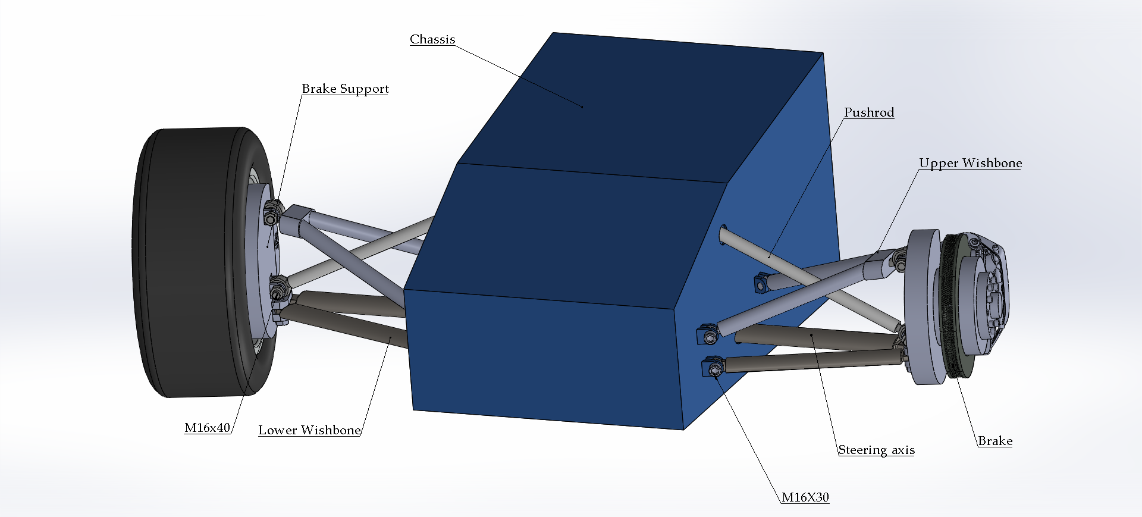
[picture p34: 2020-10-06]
Art/Front Suspension System.PNG

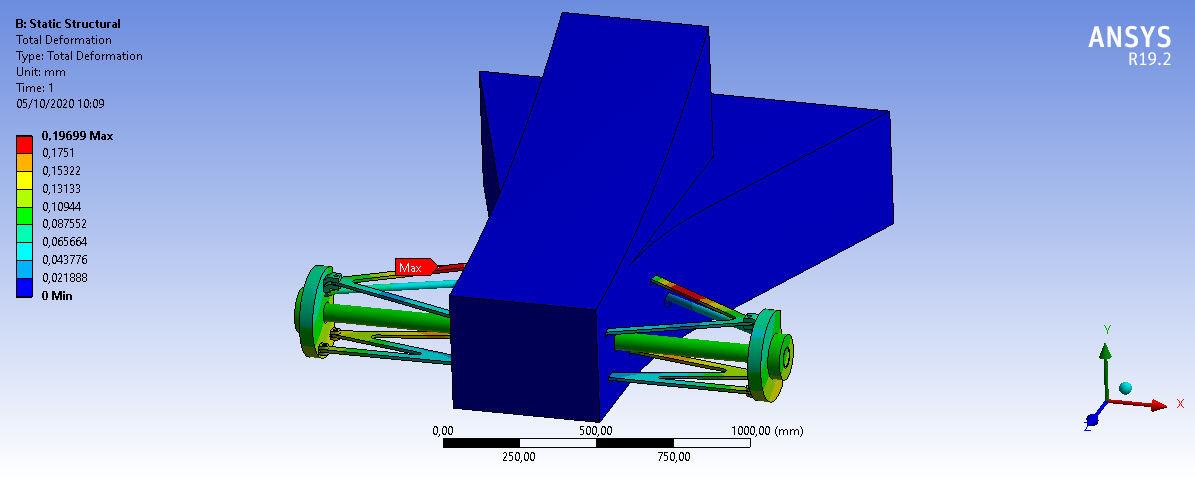
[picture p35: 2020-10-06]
Suspensions/Python/Plots/Rear_deformation.png

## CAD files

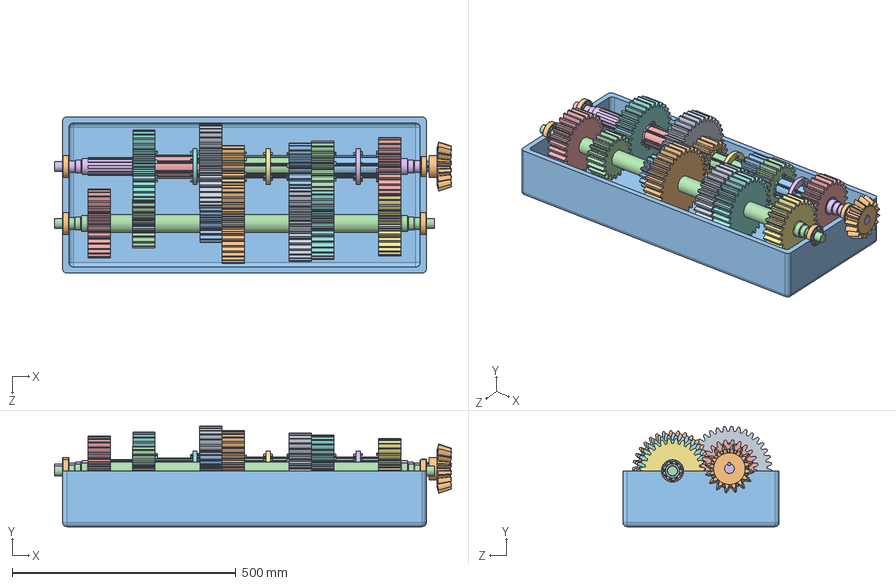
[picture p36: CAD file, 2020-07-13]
Transmission/Assemblies/Assembly_gearbox.SLDASM
888.1 x 224.9 x 350.0 mm
_62_22_PART1 x 3
_62_22_PART2 x 3
_62_22_PART3 x 27
lay_shaft
Key_50 x 3
Key_100 x 2
3_lay_shaft_Gear
4_lay_shaft_Gear
5_lay_shaft_Gear
6_lay_shaft_Gear
1_lay_shaft_Gear
2_lay_shaft_Gear
Input_gear
Main_shaft
_320_22 X_ir
_320_22 X_cage
_320_22 X_roller x 17
_320_22 X_or
Hub_1
Hub_2
Hub_3
61809-y_1 x 3
61809-y_1_2 x 3
61809-y_1_3 x 3
61809-y_1_4 x 3
61809-y_1_5 x 3
61809-y_1_6 x 3
61809-y_1_7 x 3
rnao45x62x40-zw-asr1-xl_1 x 3
rnao45x62x40-zw-asr1-xl_1_2 x 3
rnao45x62x40-zw-asr1-xl_1_3 x 3
rnao45x62x40-zw-asr1-xl_1_4 x 3
rnao45x62x40-zw-asr1-xl_1_5 x 3
rnao45x62x40-zw-asr1-xl_1_6 x 3
rnao45x62x40-zw-asr1-xl_1_7 x 3
rnao45x62x40-zw-asr1-xl_1_8 x 3
rnao45x62x40-zw-asr1-xl_1_9 x 3
rnao45x62x40-zw-asr1-xl_1_10 x 3
rnao45x62x40-zw-asr1-xl_1_11 x 3
2_Main_shaft_Gear
1_Main_shaft_Gear
6_Main_shaft_Gear
5_Main_shaft_Gear
4_Main_shaft_Gear
3_Main_shaft_Gear
Disk_3_4
Disk_5_6
Disk_1_2
Key_50_bevel
Bevel_Gear_Output
gearbox_housing

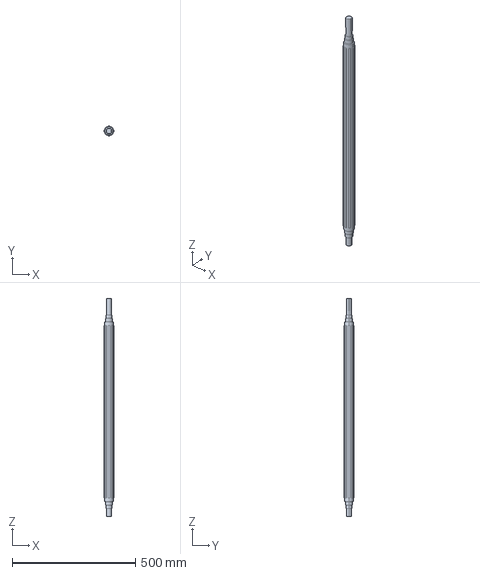
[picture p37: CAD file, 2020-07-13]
Transmission/Gearbox/Shafts/Creo/Main_Shaft/Main_shaft.stp
39.9 x 39.9 x 885.0 mm

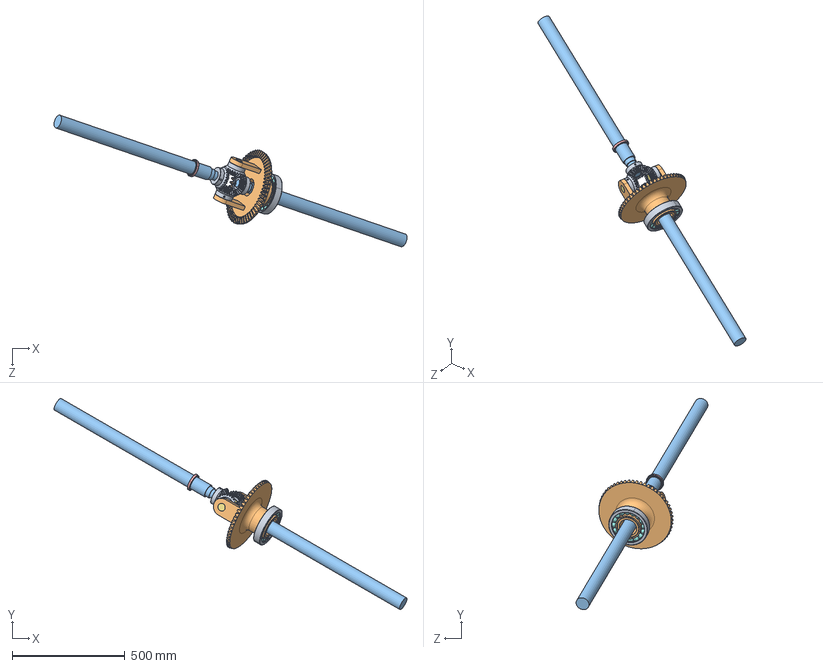
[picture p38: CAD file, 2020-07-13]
Transmission/Assemblies/Open Differential.SLDASM
1568.8 x 938.9 x 585.8 mm
SMA4_25_On_3 x 4
Gear_bevel_wheel
71907_CDTP_P4B_3 x 42
71907_CDTP_P4B_25 x 2
71907_CDTP_P4B_27 x 2
key_10_8 x 4
pin x 2
7220_BECBM_3 x 16
7220_BECBM_20
7220_BECBM_22
wheel_shaft x 2

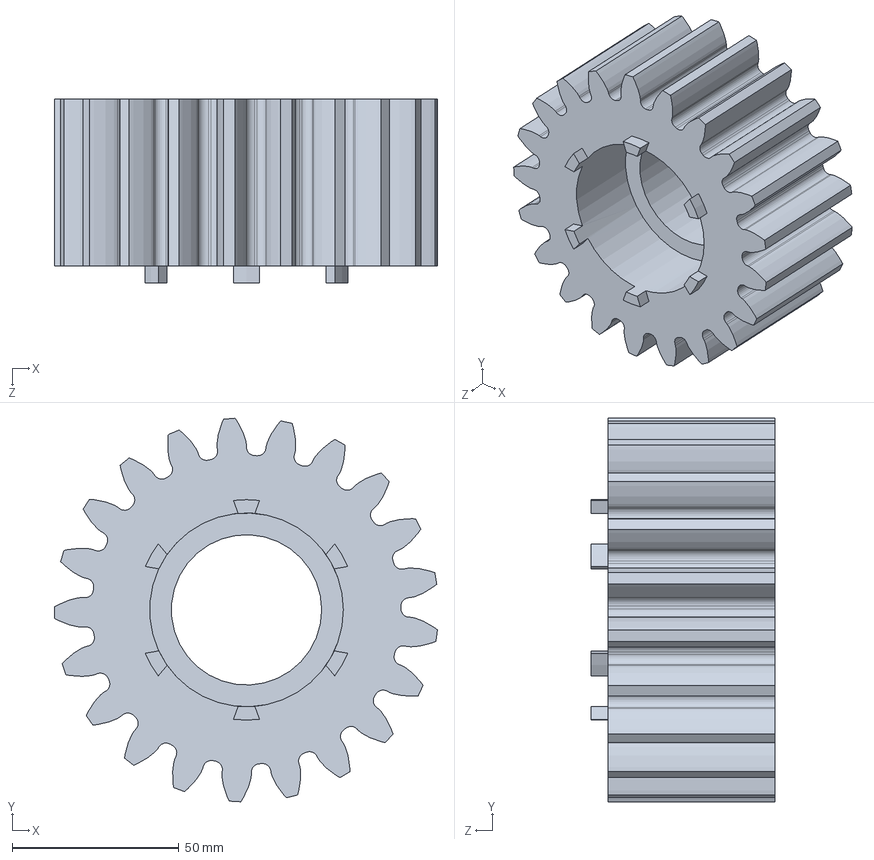
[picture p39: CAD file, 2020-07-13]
Transmission/Gearbox/Gears/SolidWorks/Main_shaft/4_Main_shaft_Gear.SLDPRT
114.7 x 114.9 x 55.0 mm

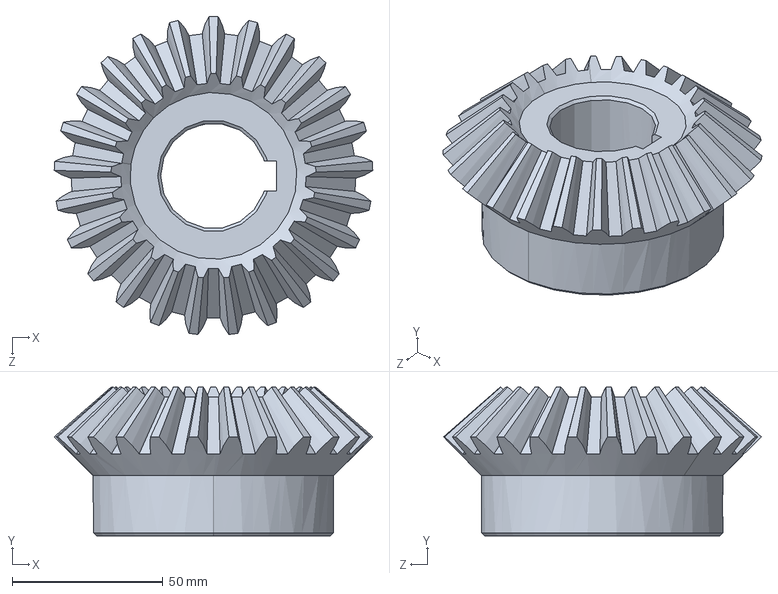
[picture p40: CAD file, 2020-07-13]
Transmission/Open Differential/Extra/Gears/Miter bevel gear/SMA4_25_On.sldasm
105.6 x 49.3 x 105.4 mm

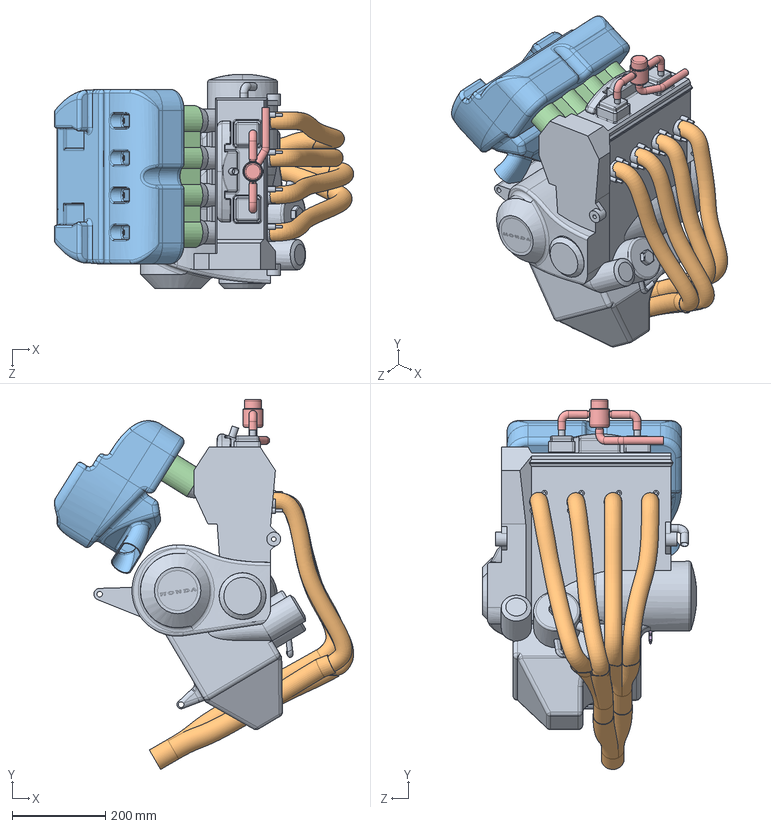
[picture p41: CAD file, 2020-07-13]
Engine (Honda CBR1000RR)/SolidWorks/Honda CBR1000RR Engine Assembly.SLDASM
643.2 x 794.9 x 458.9 mm
Hond CBR1000RR 2008 Engine_1
Exhaust pipes_1
Air Box CBR1000RR 2008_1
Throttle Body CBR1000RR 2008_1
EGR_1
Engine sprocket_1

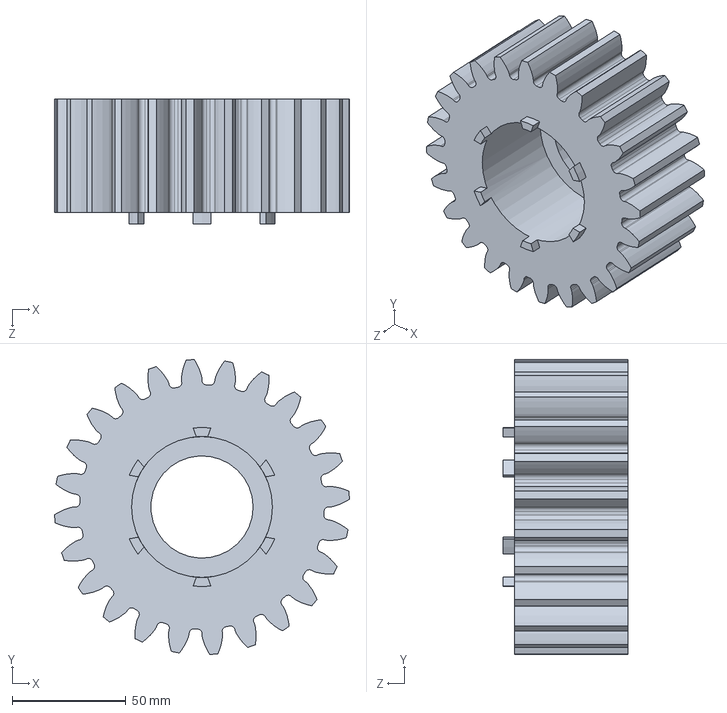
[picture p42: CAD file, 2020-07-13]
Transmission/Gearbox/Gears/SolidWorks/Main_shaft/3_Main_shaft_Gear.SLDPRT
129.8 x 129.8 x 55.0 mm

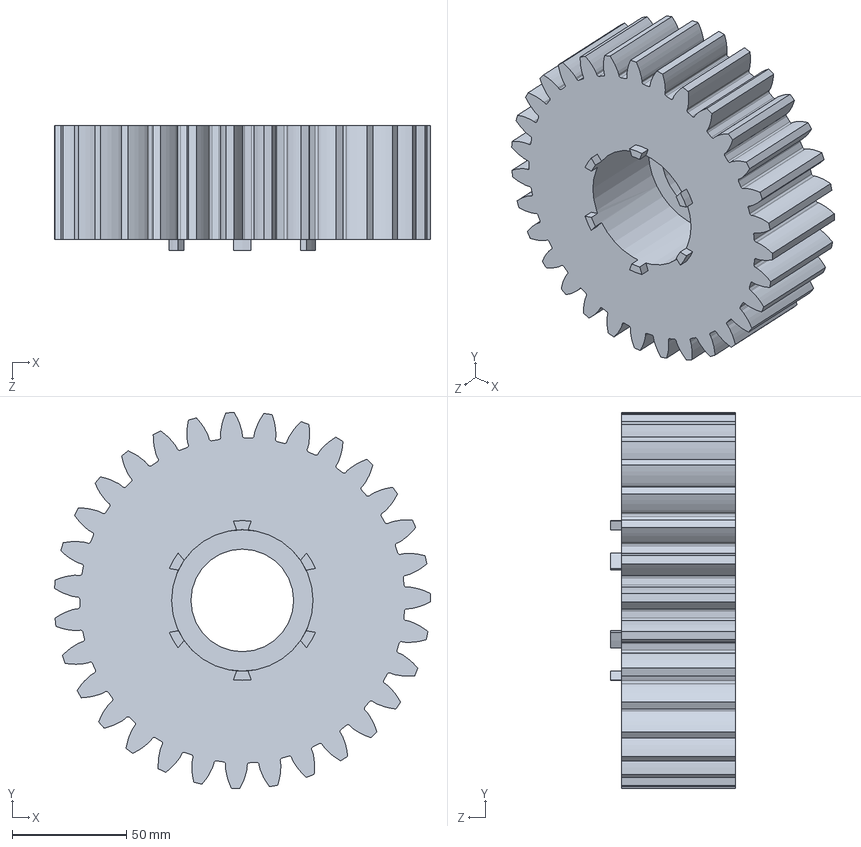
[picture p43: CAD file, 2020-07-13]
Transmission/Gearbox/Gears/SolidWorks/Main_shaft/2_Main_shaft_Gear.SLDPRT
164.8 x 164.9 x 55.0 mm

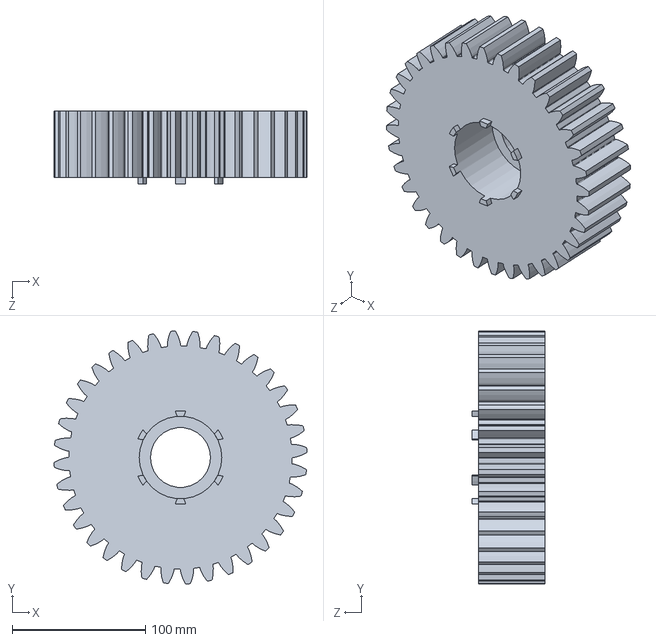
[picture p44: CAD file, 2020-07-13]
Transmission/Gearbox/Gears/SolidWorks/Main_shaft/1_Main_shaft_Gear.SLDPRT
189.9 x 189.9 x 55.0 mm

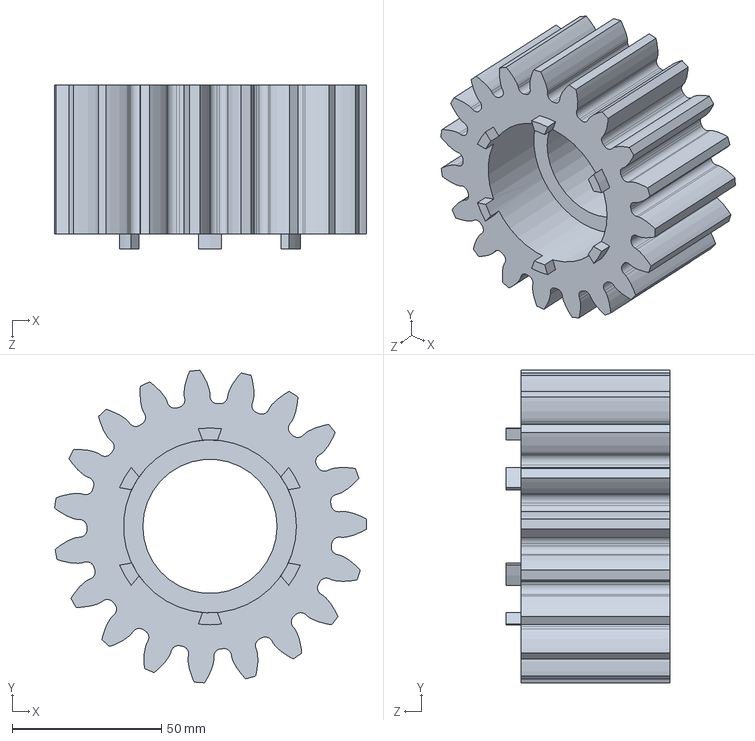
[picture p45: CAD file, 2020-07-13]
Transmission/Gearbox/Gears/SolidWorks/Main_shaft/5_Main_shaft_Gear.SLDPRT
104.6 x 104.9 x 55.0 mm

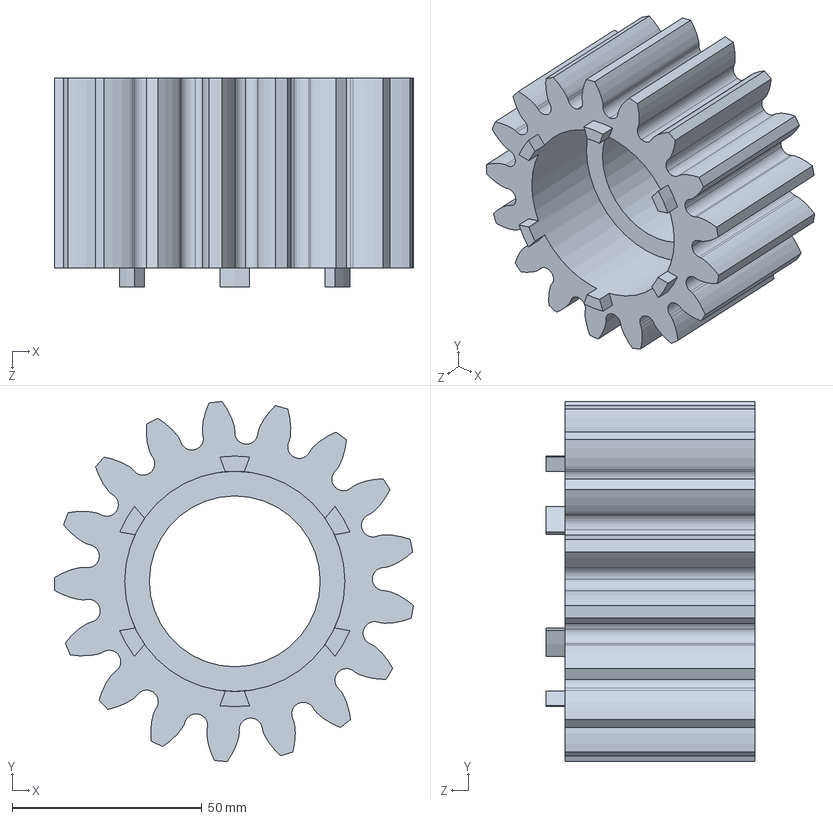
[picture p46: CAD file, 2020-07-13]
Transmission/Gearbox/Gears/SolidWorks/Main_shaft/6_Main_shaft_Gear.SLDPRT
94.6 x 94.8 x 55.0 mm

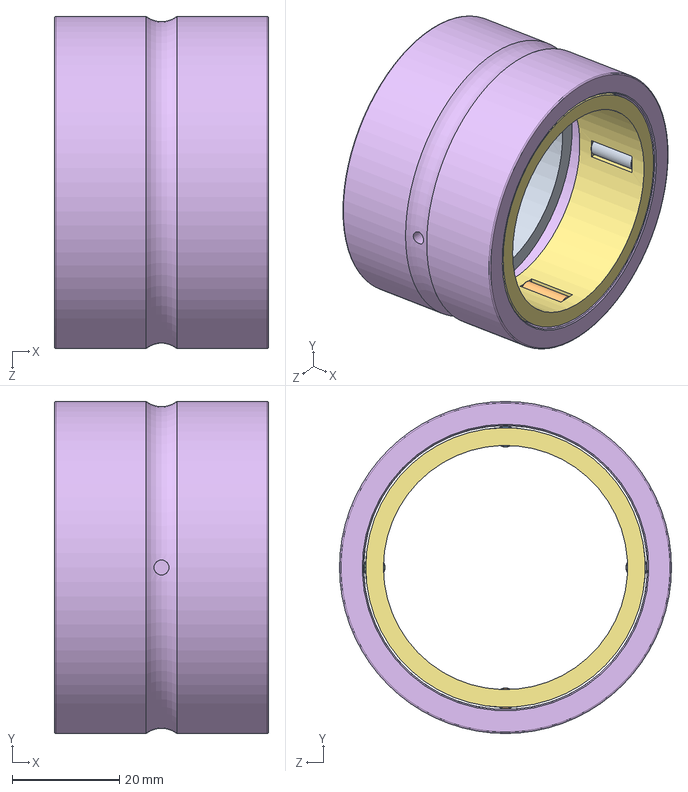
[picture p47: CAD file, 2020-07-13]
Transmission/Gearbox/Bearings/SolidWorks/rnao45x62x40-zw-asr1-xl.SLDASM
40.0 x 62.0 x 62.0 mm
rnao45x62x40-zw-asr1-xl_1
rnao45x62x40-zw-asr1-xl_1_2
rnao45x62x40-zw-asr1-xl_1_3
rnao45x62x40-zw-asr1-xl_1_4
rnao45x62x40-zw-asr1-xl_1_5
rnao45x62x40-zw-asr1-xl_1_6
rnao45x62x40-zw-asr1-xl_1_7
rnao45x62x40-zw-asr1-xl_1_8
rnao45x62x40-zw-asr1-xl_1_9
rnao45x62x40-zw-asr1-xl_1_10
rnao45x62x40-zw-asr1-xl_1_11

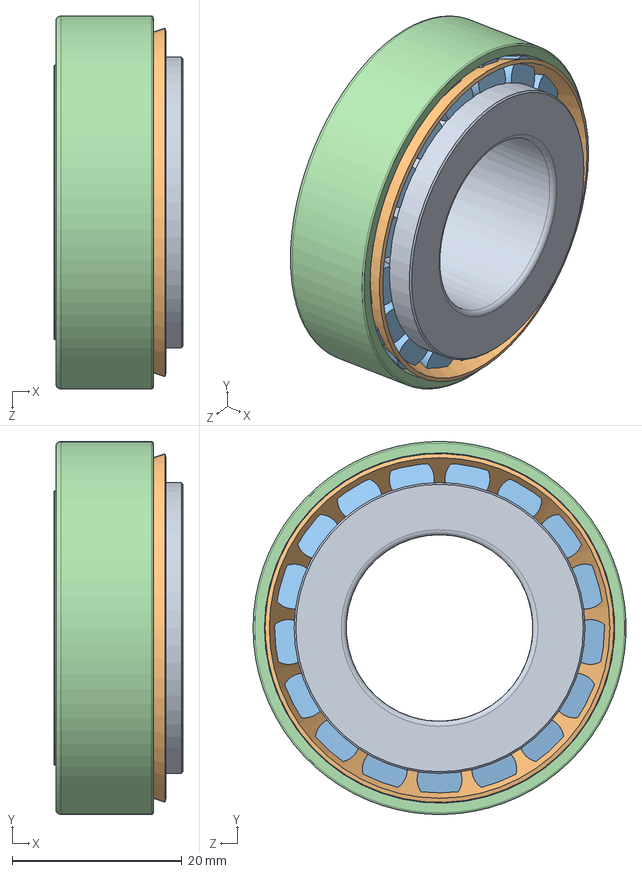
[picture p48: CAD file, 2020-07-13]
Transmission/Gearbox/Bearings/SolidWorks/SKF_320_22 X.SLDASM
15.2 x 44.0 x 44.0 mm
_320_22 X_ir
_320_22 X_cage
_320_22 X_roller x 17
_320_22 X_or

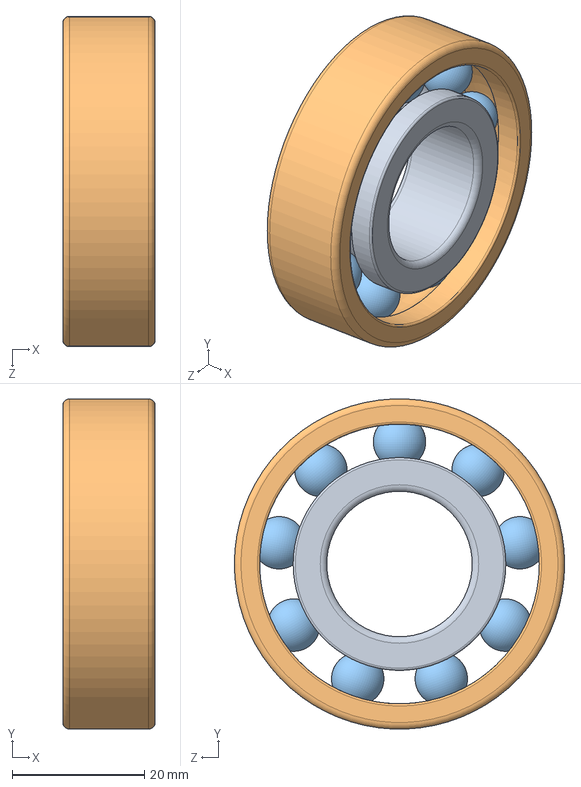
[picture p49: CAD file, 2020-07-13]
Transmission/Gearbox/Bearings/SolidWorks/SKF_62_22.SLDASM
14.0 x 50.0 x 50.0 mm
_62_22_PART1
_62_22_PART2
_62_22_PART3 x 9

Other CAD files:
Suspensions/Bearings/SOLIDWORKS/6314.sldasm
Transmission/Open Differential/Extra/Bearings/71907 CDTP_P4B/Backup (1) of 71907_CDTP_P4B.sldasm
Transmission/Gearbox/Shafts/SolidWorks/Main_shaft.SLDPRT
Transmission/Open Differential/Extra/Bearings/7220_BECBM/7220_BECBM.sldasm
Engine (Honda CBR1000RR)/SolidWorks/Air Box CBR1000RR 2008_1.sldprt
Engine (Honda CBR1000RR)/SolidWorks/EGR_1.sldprt
Engine (Honda CBR1000RR)/SolidWorks/Engine sprocket_1.sldprt
Engine (Honda CBR1000RR)/SolidWorks/Exhaust pipes_1.sldprt
Engine (Honda CBR1000RR)/SolidWorks/Hond CBR1000RR 2008 Engine_1.sldprt
Engine (Honda CBR1000RR)/SolidWorks/Throttle Body CBR1000RR 2008_1.sldprt
Suspensions/Bearings/SOLIDWORKS/6314_12.sldprt
Suspensions/Bearings/SOLIDWORKS/6314_21.sldprt
Suspensions/Bearings/SOLIDWORKS/6314_23.sldprt
Suspensions/Catia/Brake_support.CATPart
Suspensions/Catia/Brake_support_rear.CATPart
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

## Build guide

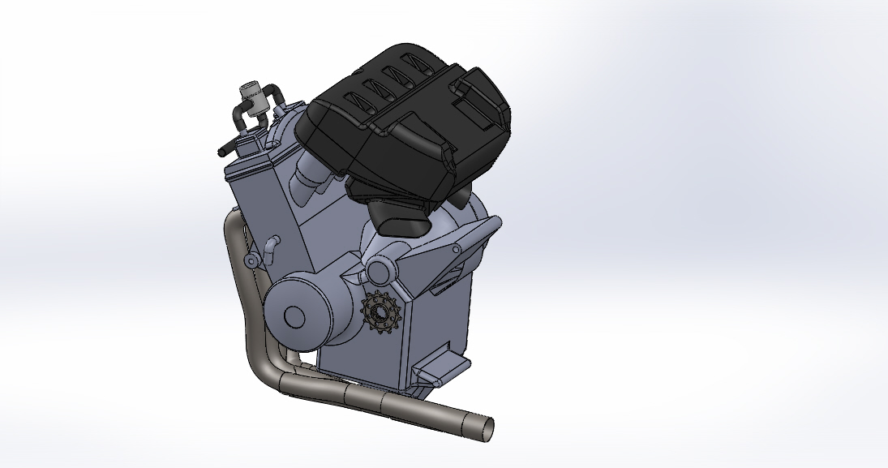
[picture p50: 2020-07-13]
Engine (Honda CBR1000RR)/Honda CBR1000RR Engine Assembly.JPG

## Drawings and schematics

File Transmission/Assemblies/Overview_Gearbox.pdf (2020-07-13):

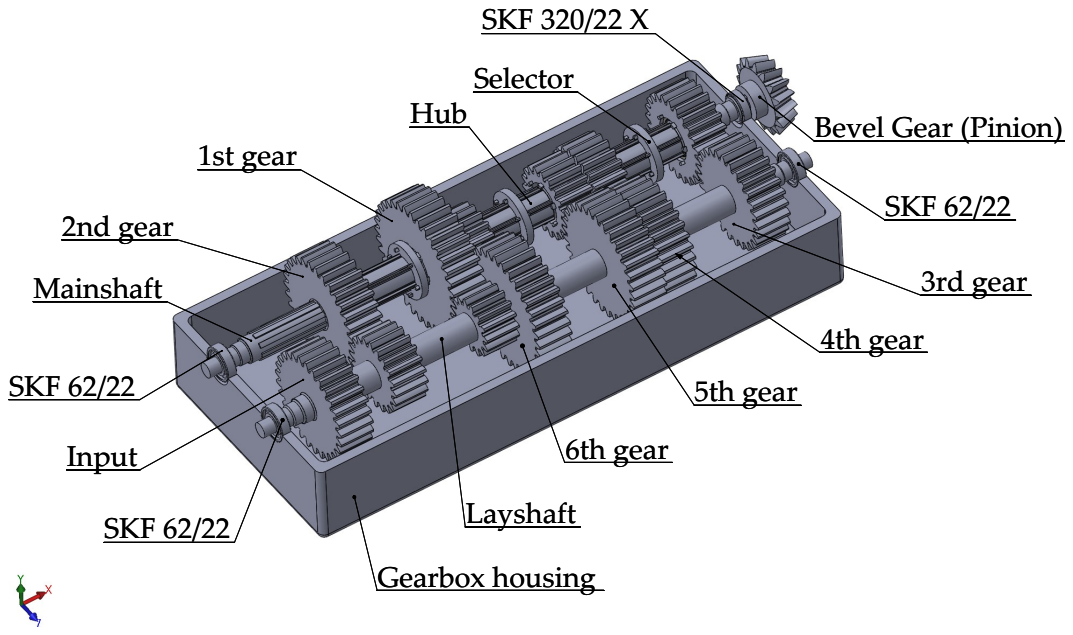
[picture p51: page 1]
Mainshaft; Layshaft; Input; 2nd gear; 1st gear; 5th gear; 4th gear; 3rd gear; 6th gear; Selector; Hub; SKF 320/22 X; SKF 62/22; Gearbox housing

Bevel Gear (Pinion)

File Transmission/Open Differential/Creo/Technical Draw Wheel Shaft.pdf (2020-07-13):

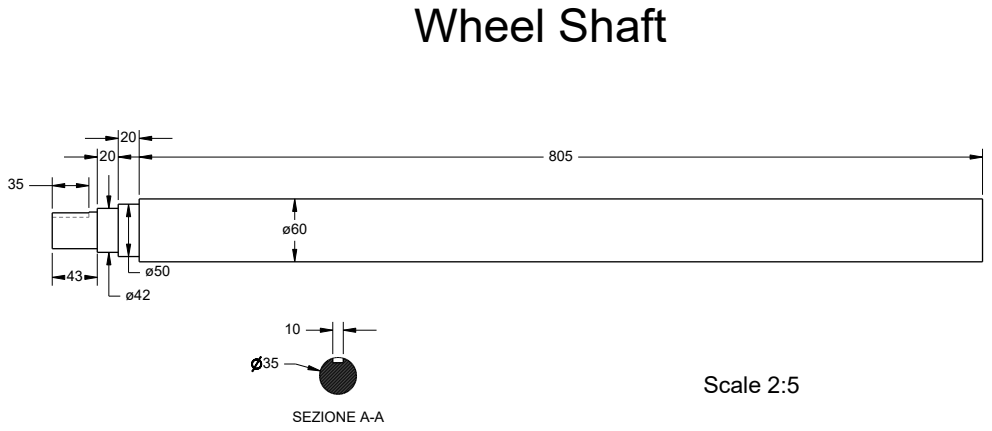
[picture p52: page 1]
Scale 2:5; Wheel Shaft; SEZIONE A-A

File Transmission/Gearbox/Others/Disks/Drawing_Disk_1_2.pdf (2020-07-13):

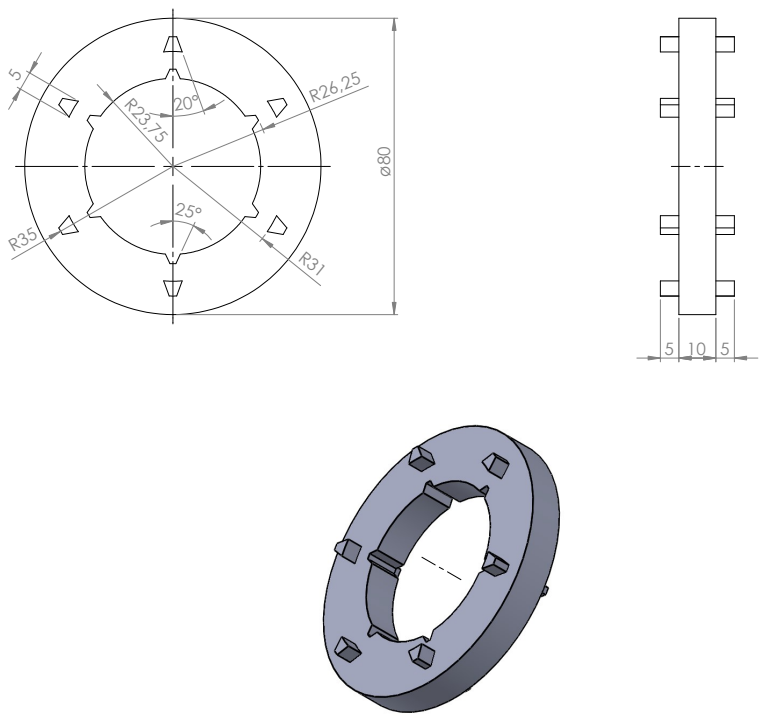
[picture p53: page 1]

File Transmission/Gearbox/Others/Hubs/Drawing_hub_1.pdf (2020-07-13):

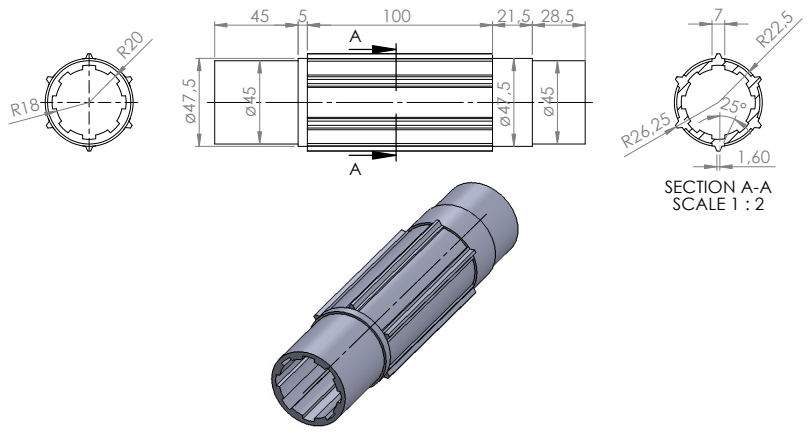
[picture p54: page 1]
28,5 ø⁴⁷,5; 21,5 ø⁴⁷,5; ø⁴⁵ AA R20 R18; SECTION A-A; SCALE 1 : 2R2

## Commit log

2020-07-14 Create Nuovo documento di testo.txt
2020-07-14 Bearing update
2020-10-06 Suspension added
    Chapter 4 Suspension added to the report + fixed some small error from the previous release
    [07170-16x70.SLDPRT, 10_00_0934_0016_001.SLDPRT, 1952 CS 6X28_5X80.sldprt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]
